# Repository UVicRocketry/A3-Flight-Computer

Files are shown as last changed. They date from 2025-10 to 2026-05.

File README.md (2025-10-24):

# A3-Flight-Computer
Hardware and software for Anduril-3 flight computer.

## Hardware 
All hardware is designed in KiCAD. If any footprints are added create a folder with the component name in the component-library folder and export all the files to there. when importing footprints and symbols add them to the A3-Flight-Computer library in KiCAD A3 Also add any datasheet and relevent documentation to this folder. 

## Software
All software will be stored in the A3-Flight-Computer-Software. (Rest of Organization TBD)

Various resources such as application notes, various datasheets etc will be stored in the resource folder

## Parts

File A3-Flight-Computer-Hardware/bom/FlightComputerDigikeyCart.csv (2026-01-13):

Index | Quantity | Part Number | Manufacturer Part Number | Description | Customer Reference | Available | Backorder | Unit Price | Extended Price CAD
1 | 2 | 670-1528-1-ND | ST1W008S4ER1500 | CONN MICRO SD CARD R/A SMD | J2 | 2 | 0 | 2.72000 | 5.44
2 | 2 | SER4070CT-ND | TSX-3225 16.0000MF18X-AC0 | CRYSTAL 16.0000MHZ 9PF SMD | Y1 | 2 | 0 | 0.57000 | 1.14
3 | 2 | XC2160CT-ND | ECS-.327-9-34QCS-TR | CRYSTAL 32.7680KHZ 9PF SMD | Y2 | 2 | 0 | 1.37000 | 2.74
4 | 2 | 497-STM32H523RET6-ND | STM32H523RET6 | IC MCU 32BIT 512KB FLASH 64LQFP | U1 | 2 | 0 | 7.17000 | 14.34
5 | 3 | AZ1117CH-3.3TRG1DICT-ND | AZ1117CH-3.3TRG1 | IC REG LINEAR 3.3V 1A SOT-223-3 | VR1 | 3 | 0 | 0.25000 | 0.75
6 | 2 | 2073-USB4105-GF-ACT-ND | USB4105-GF-A | CONN RCP USB2.0 TYP C 16P SMD RA | J3 | 2 | 0 | 1.13000 | 2.26
7 | 2 | 401-1999-1-ND | JS102011SAQN | SWITCH SLIDE SPDT 300MA 6V | SW1 | 2 | 0 | 1.10000 | 2.20
8 | 2 | 490-PKMCS0909E48H0-R1CT-ND | PKMCS0909E48H0-R1 | BUZZER PIEZO 2.5V 9X9MM W SMD | BZ1 | 2 | 0 | 1.63000 | 3.26
9 | 2 | IRLML0030TRPBFCT-ND | IRLML0030TRPBF | MOSFET N-CH 30V 5.3A SOT23 | Q1 | 2 | 0 | 0.72000 | 1.44
10 | 10 | 1655-DSS14UCT-ND | DSS14U | DIODE SCHOTTKY 40V 1A SOD123FL | D1, D2, D6 | 10 | 0 | 0.17100 | 1.71
11 | 2 | 160-1179-1-ND | LTST-C170GKT | LED GREEN CLEAR SMD | D4 | 2 | 0 | 0.15000 | 0.30
12 | 2 | 160-1413-1-ND | LTST-C170KFKT | LED ORANGE CLEAR SMD | D3 | 2 | 0 | 0.20000 | 0.40
13 | 2 | 296-TCAN3414DRCT-ND | TCAN3414DR | IC TRANSCEIVER HALF 1/1 8SOIC | U5 | 2 | 0 | 2.40000 | 4.80
14 | 2 | ADXL375BCCZ-RL7CT-ND | ADXL375BCCZ-RL7 | ACCELEROMETER 200G I2C/SPI 14LGA | U2 | 2 | 0 | 19.13000 | 38.26
15 | 2 | 497-LSM6DSO32CT-ND | LSM6DSO32TR | INEMO INERTIAL MODULE: 3D ACCELE | U3 | 2 | 0 | 5.40000 | 10.80
16 | 2 | 497-16265-1-ND | LPS22HBTR | SENSOR 18.27PSIA 24BIT 10HLGA | U4 | 2 | 0 | 3.78000 | 7.56
17 | 4 | 18-SMF54CACT-ND | SMF54CA | TVS DIODE 54VWM 87.1VC SOD123F | D7, D8 | 4 | 0 | 0.58000 | 2.32
18 | 3 | 2449-CS1213AGF260CT-ND | CS1213AGF260 | SWITCH TACTILE SPST-NO 0.05A 50V | Sw2 | 3 | 0 | 0.60000 | 1.80
19 | 4 | 1276-1244-1-ND | CL21A475KAQNNNE | CAP CER 4.7UF 25V X5R 0805 | C1 | 4 | 0 | 0.14000 | 0.56
20 | 3 | 1276-CL21A226MAYNNNECT-ND | CL21A226MAYNNNE | CAP CER 22UF 25V X5R 0805 | C8 | 3 | 0 | 0.12000 | 0.36
21 | 3 | 1276-2872-1-ND | CL21B106KOQNNNE | CAP CER 10UF 16V X7R 0805 | C9 | 3 | 0 | 0.12000 | 0.36
22 | 40 | 1276-1043-1-ND | CL05A104KA5NNNC | CAP CER 0.1UF 25V X5R 0402 | C2-7, C10, C17-24 | 40 | 0 | 0.00300 | 0.12
23 | 10 | 490-10012-1-ND | GRM155C80J225KE95D | CAP CER 2.2UF 6.3V X6S 0402 | C13, C14 | 10 | 0 | 0.07800 | 0.78
24 | 10 | 490-5926-1-ND | GRM1555C1H160JA01D | CAP CER 16PF 50V C0G/NP0 0402 | C15, C16 | 10 | 0 | 0.06400 | 0.64
25 | 10 | 1276-CL05C080DB51PNCCT-ND | CL05C080DB51PNC | CAP CER 8PF 50V C0G/NP0 0402 | C11, C12 | 10 | 0 | 0.04300 | 0.43
26 | 10 | 478-KGM05AR71E472KHCT-ND | KGM05AR71E472KH | CAP CER 4700PF 25V X7R 0402 | C25 | 10 | 0 | 0.03500 | 0.35
27 | 10 | P100KLCT-ND | ERJ-2RKF1003X | RES 100K OHM 1% 1/10W 0402 | R10 | 10 | 0 | 0.04300 | 0.43
28 | 10 | RMCF0402FT10K0CT-ND | RMCF0402FT10K0 | RES 10K OHM 1% 1/16W 0402 | R6 | 10 | 0 | 0.01100 | 0.11
29 | 10 | P100LCT-ND | ERJ-2RKF1000X | RES SMD 100 OHM 1% 1/10W 0402 | R9 | 10 | 0 | 0.04300 | 0.43
30 | 10 | P240LCT-ND | ERJ-2RKF2400X | RES SMD 240 OHM 1% 1/10W 0402 | R5, R7, R8 | 10 | 0 | 0.04300 | 0.43
31 | 6 | P5.1KDCCT-ND | ERA-2AEB512X | RES SMD 5.1K OHM 0.1% 1/16W 0402 | R1, R2 | 6 | 0 | 0.15000 | 0.90
32 | 10 | YAG3086CT-ND | RC0402FR-0727RL | RES 27 OHM 1% 1/16W 0402 | R3, R4 | 10 | 0 | 0.01100 | 0.11
33 | 10 | RMCF0402FT1K80CT-ND | RMCF0402FT1K80 | RES 1.8K OHM 1% 1/16W 0402 | R11, R12 | 10 | 0 | 0.00800 | 0.08
34 | 10 | 455-S2B-XH-A-ND | S2B-XH-A | CONN HEADER R/A 2POS 2.5MM | J1, J4, J6, J8 | 10 | 0 | 0.14800 | 1.48
35 | 3 | 455-S3B-XH-A-ND | S3B-XH-A | CONN HEADER R/A 3POS 2.5MM | J7 | 3 | 0 | 0.22000 | 0.66
36 | 2 | 160-1427-1-ND | LTST-C171KRKT | LED RED CLEAR SMD | D5 | 2 | 0 | 0.20000 | 0.40
37 | 10 | P59.0LCT-ND | ERJ-2RKF59R0X | RES SMD 59 OHM 1% 1/10W 0402 | R14, R13 | 10 | 0 | 0.04300 | 0.43
38 | 2 | 296-28778-1-ND | TLV1117LV33DCYR | IC REG LINEAR 3.3V 1A SOT-223-4 |  | 2 | 0 | 0.38656 | 0.78
39 | 10 | 1276-1029-1-ND | CL21B105KBFNNNE | CAP CER 1UF 50V X7R 0805 |  | 10 | 0 | 0.01859 | 0.19
40 | 2 | SAM8996-ND | TSW-104-07-F-D | CONN HEADER VERT 8POS 2.54MM | DEBUG | 2 | 0 | 0.62185 | 1.24

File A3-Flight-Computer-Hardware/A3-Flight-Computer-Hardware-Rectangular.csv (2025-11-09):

Reference | Qty | Value | DNP | Exclude from BOM | Exclude from Board | Footprint | Datasheet
BZ1 | 1 | Buzzer |  |  |  | Buzzer_Beeper:Buzzer_Murata_PKMCS0909E | ~
C1 | 1 | 4.7uF |  |  |  | Capacitor_SMD:C_0805_2012Metric
C2,C3,C4,C5,C6,C9,C16,C17,C18,C19,C20,C21,C22,C23 | 14 | 100nF |  |  |  | Capacitor_SMD:C_0805_2012Metric
C7 | 1 | 22uF |  |  |  | Capacitor_SMD:C_0805_2012Metric
C8 | 1 | 10uF |  |  |  | Capacitor_SMD:C_0805_2012Metric
C10,C11 | 2 | 8pF |  |  |  | Capacitor_SMD:C_0805_2012Metric
C12,C13 | 2 | 2.2uF |  |  |  | Capacitor_SMD:C_0805_2012Metric
C14 | 1 | 16pF |  |  |  | Capacitor_SMD:C_0805_2012Metric
C15 | 1 | 16pf |  |  |  | Capacitor_SMD:C_0805_2012Metric
C24 | 1 | 4.7nF |  |  |  | Capacitor_SMD:C_0805_2012Metric
D1,D2 | 2 | DSS14U |  |  |  | Diode_SMD:D_SOD-123
D3,D4 | 2 | LED |  |  |  | LED_SMD:LED_0805_2012Metric_Pad1.15x1.40mm_HandSolder | ~
D5 | 1 | SS14 |  |  |  | Diode_SMD:D_SMA | https://www.vishay.com/docs/88746/ss12.pdf
D6,D7 | 2 | SMF54CA |  |  |  | Diode_SMD:D_SMF | https://www.littelfuse.com/media?itemid=75e32973-b177-4ee3-a0ff-cedaf1abdb93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
J1 | 1 | BAT |  |  |  | Connector_JST:JST_XH_S2B-XH-A_1x02_P2.50mm_Horizontal | ~
J2 | 1 | ST1W008S4ER1500 |  |  |  | A3-Flight-Computer:JAE_ST1W008S4ER1500
J3 | 1 | USB_C_Receptacle_USB2.0_14P |  |  |  | Connector_USB:USB_C_Receptacle_Palconn_UTC16-G | https://www.usb.org/sites/default/files/documents/usb_type-c.zip
J4 | 1 | Debug Header |  |  |  | Connector_PinHeader_2.54mm:PinHeader_2x03_P2.54mm_Vertical | ~
J5 | 1 | Cam 1 |  |  |  | Connector_JST:JST_XH_B2B-XH-A_1x02_P2.50mm_Vertical | ~
J6 | 1 | Cam 2 |  |  |  | Connector_JST:JST_XH_B2B-XH-A_1x02_P2.50mm_Vertical | ~
J8 | 1 | Telem |  |  |  | Connector_JST:JST_XH_B3B-XH-A_1x03_P2.50mm_Vertical | ~
J9 | 1 | CAN |  |  |  | Connector_JST:JST_XH_S2B-XH-A_1x02_P2.50mm_Horizontal | ~
Q1 | 1 | IRLML0030 |  |  |  | Package_TO_SOT_SMD:SOT-23 | https://www.infineon.com/dgdl/irlml0030pbf.pdf?fileId=5546d462533600a401535664773825df
R1,R2 | 2 | 5.1K |  |  |  | Resistor_SMD:R_0805_2012Metric | ~
R3,R4 | 2 | 27R |  |  |  | Resistor_SMD:R_0805_2012Metric | ~
R5,R7 | 2 | 240R |  |  |  | Resistor_SMD:R_0805_2012Metric | ~
R6 | 1 | 10k |  |  |  | Resistor_SMD:R_0805_2012Metric | ~
R8 | 1 | 100 |  |  |  | Resistor_SMD:R_0805_2012Metric | ~
R9 | 1 | 100k |  |  |  | Resistor_SMD:R_0805_2012Metric | ~
R10,R11 | 2 | 1.8k |  |  |  | Resistor_SMD:R_0805_2012Metric | ~
R12,R13 | 2 | 60 |  |  |  | Resistor_SMD:R_0805_2012Metric | ~
SW1 | 1 | BOOT |  |  |  | Button_Switch_SMD:SW_SPDT_CK_JS102011SAQN | ~
SW2 | 1 | RST |  |  |  | Button_Switch_SMD:SW_SPST_TS-1088-xR025 | ~
U1 | 1 | STM32H523RETx |  |  |  | Package_QFP:LQFP-64_10x10mm_P0.5mm | https://www.st.com/resource/en/datasheet/stm32h523re.pdf
U2 | 1 | ADXL375BCCZ-RL7 |  |  |  | A3-Flight-Computer:LGA_CC-14-1_ADI | https://www.analog.com/media/en/technical-documentation/data-sheets/ADXL375-EP.pdf
U3 | 1 | LSM6DSO32TR |  |  |  | A3-Flight-Computer:XDCR_LSM6DSO32TR
U4 | 1 | LPS22HBTR |  |  |  | A3-Flight-Computer:PQFN50P200X200X80-10N
U5 | 1 | PTCAN3414DR |  |  |  | A3-Flight-Computer:SOIC8_D_TEX | https://www.ti.com/lit/gpn/tcan3414
VR1 | 1 | AZ1117CH-3.3TRG1 |  |  |  | A3-Flight-Computer:VREG_AZ1117CH-3.3TRG1
Y1 | 1 | TSX-3225_16.0000MF18X-AC0 |  |  |  | A3-Flight-Computer:XTAL_TSX-3225_16.0000MF18X-AC0
Y2 | 1 | ECS-.327-9-34QCS-TR |  |  |  | A3-Flight-Computer:XTAL_ECS-.327-9-34QCS-TR

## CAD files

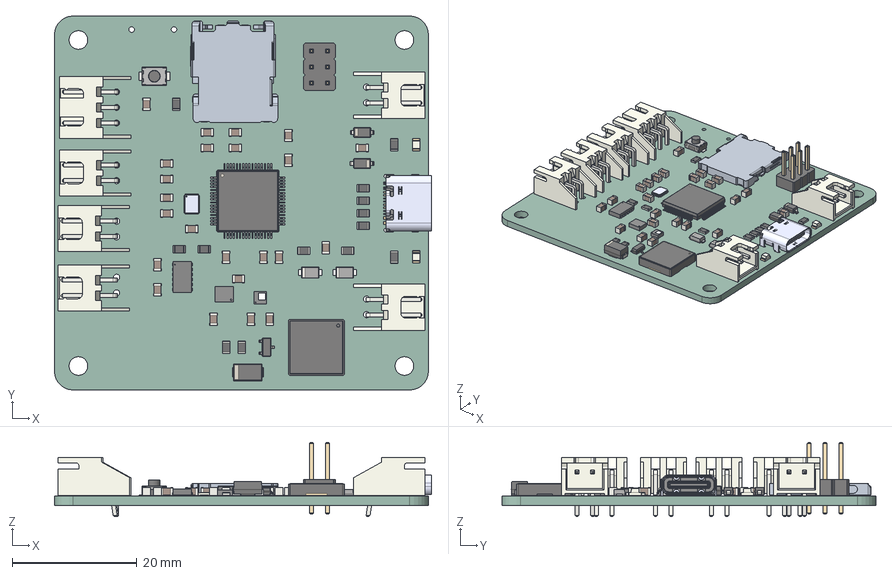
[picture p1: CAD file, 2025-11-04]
A3-Flight-Computer-Hardware/alt-design/A3-Flight-Computer-Hardware.step
60.5 x 60.0 x 11.9 mm
C_0805_2012Metric x 23
LSM6DSO32TR
R_0805_2012Metric x 13
TSX-3225_16.0000MF18X-AC0
SW_SPST_TS-1088-xR025
USB4105GFA_USB4105GFA
JST_XH_S2B-XH-A_1x02_P2.50mm_Horizontal x 5
D_SMF x 2
D_SOD-123 x 2
ST1W008S4E-V1_JAE_Proprietary
PinHeader_2x03_P2.54mm_Vertical
LED_0805_2012Metric x 2
JST_XH_S3B-XH-A_1x03_P2.50mm_Horizontal
LQFP-64_10x10mm_P0.5mm
Buzzer_Murata_PKMCS0909E
LGA_CC-14-1_ADI
LPS22HBTR
SOT-23
D_SMA
A3-Flight-Computer-Hardware_PCB

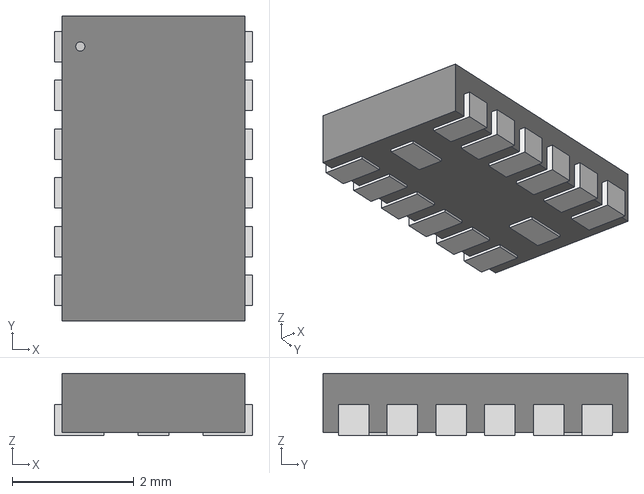
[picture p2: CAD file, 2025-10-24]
A3-Flight-Computer-Hardware/component-library/ADXL375/LGA_CC-14-1_ADI.step
3.25 x 5.00 x 1.02 mm

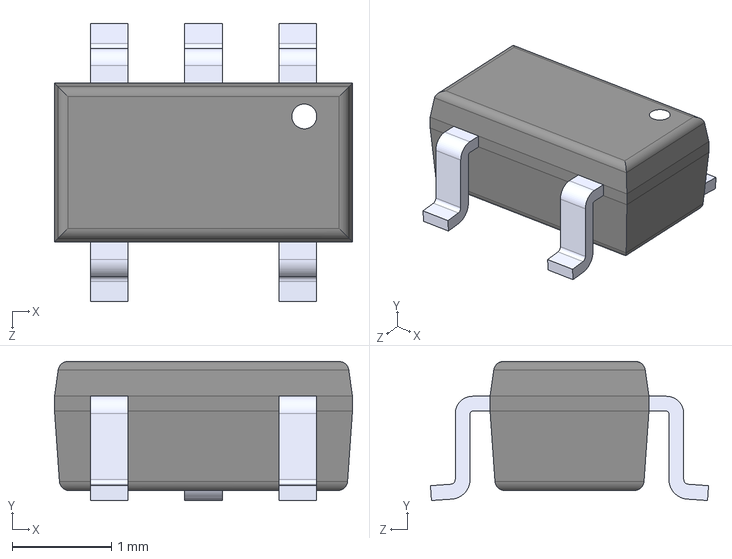
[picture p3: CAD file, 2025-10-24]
A3-Flight-Computer-Hardware/component-library/AP2112K-3.3TRG1/AP2112K-3.3TRG1.step
3.00 x 1.40 x 2.80 mm

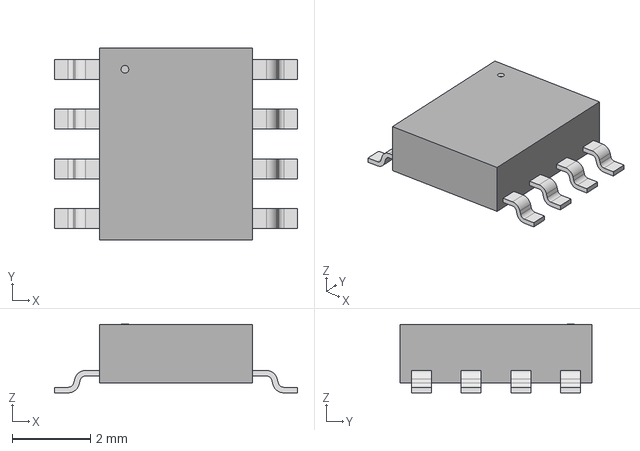
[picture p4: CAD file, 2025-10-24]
A3-Flight-Computer-Hardware/component-library/ATA6561/SOIC8_4P9X3P9MC_MCH.step
6.20 x 4.90 x 1.75 mm

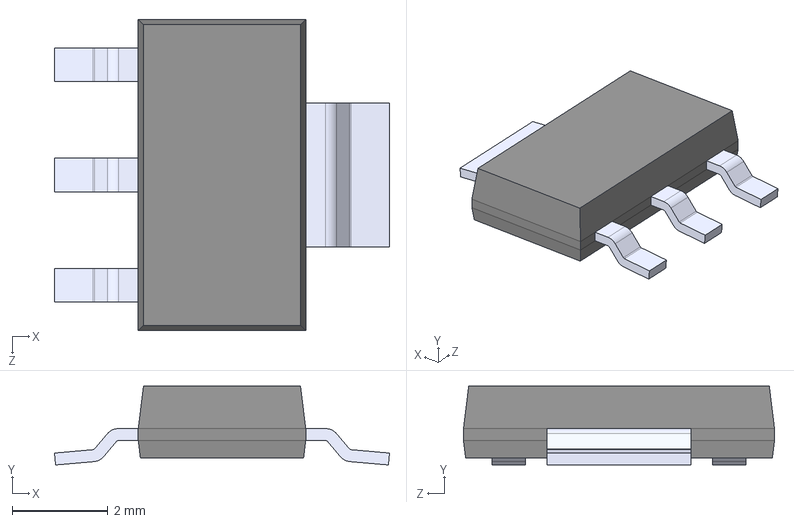
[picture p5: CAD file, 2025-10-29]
A3-Flight-Computer-Hardware/component-library/AZ1117CH-3.3TRG1/AZ1117CH-3.3TRG1.step
7.00 x 1.65 x 6.50 mm

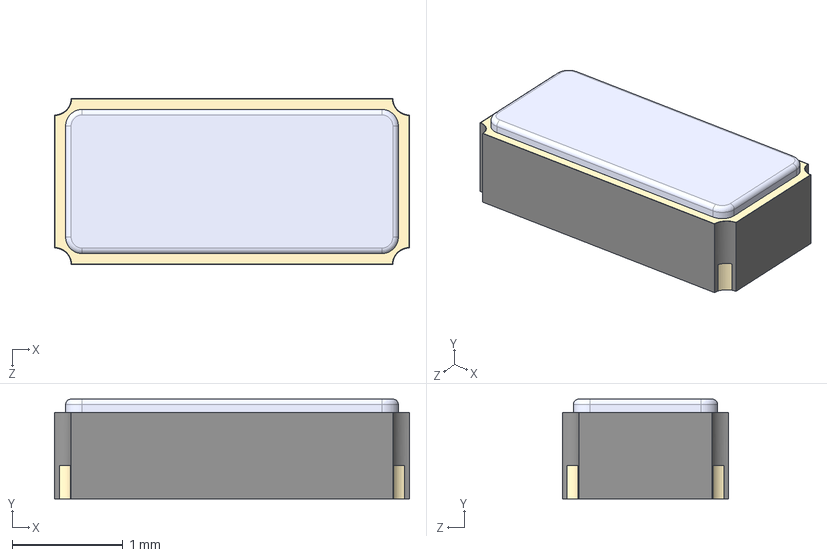
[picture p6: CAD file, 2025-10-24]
A3-Flight-Computer-Hardware/component-library/ECS-327-9-34QCS-TR/ECS-.327-9-34QCS-TR.step
3.20 x 0.9 x 1.50 mm

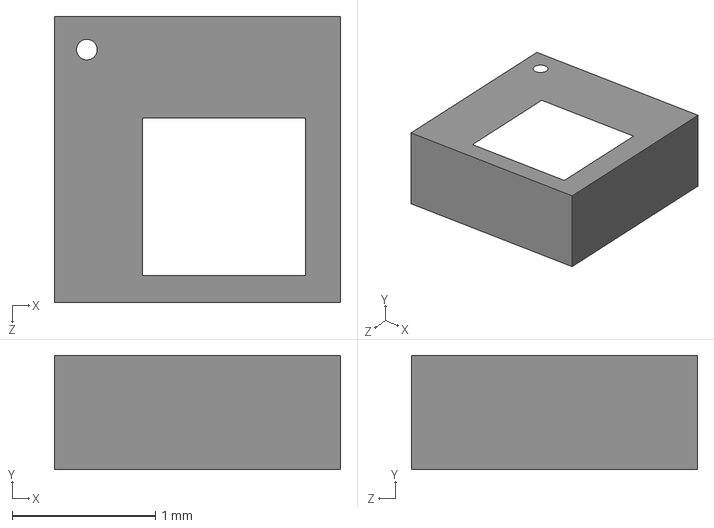
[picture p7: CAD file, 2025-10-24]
A3-Flight-Computer-Hardware/component-library/LPS22HBTR/LPS22HBTR.step
2.00 x 0.8 x 2.00 mm

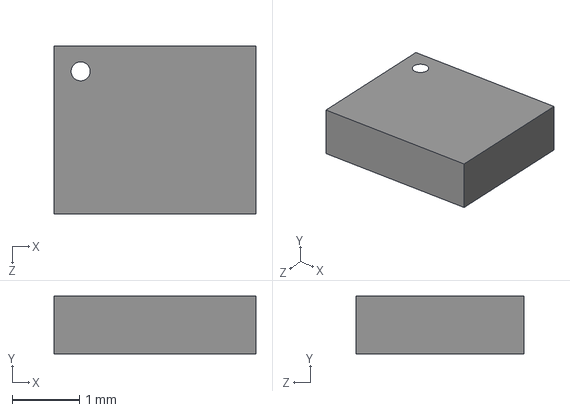
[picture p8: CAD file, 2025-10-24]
A3-Flight-Computer-Hardware/component-library/LSM6DSO32TR/LSM6DSO32TR.step
3.00 x 0.86 x 2.50 mm

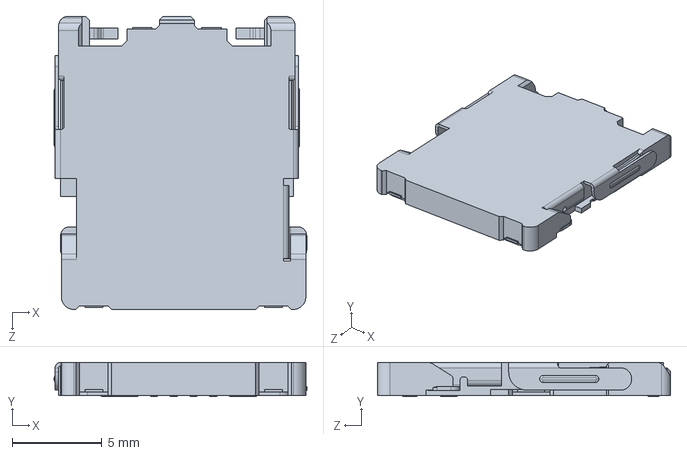
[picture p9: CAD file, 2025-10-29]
A3-Flight-Computer-Hardware/component-library/STW008S4ER1500/ST1W008S4E-V1_JAE_Proprietary.step
14.0 x 1.90 x 16.3 mm

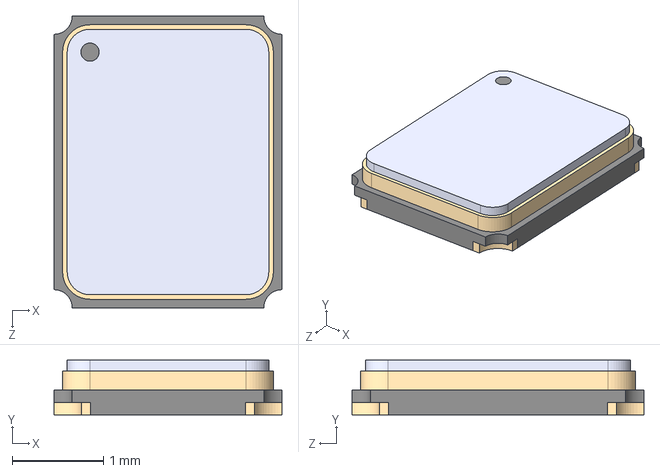
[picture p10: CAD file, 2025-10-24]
A3-Flight-Computer-Hardware/component-library/TSX-3225/TSX-3225_16.0000MF18X-AC0.step
2.50 x 0.6 x 3.20 mm

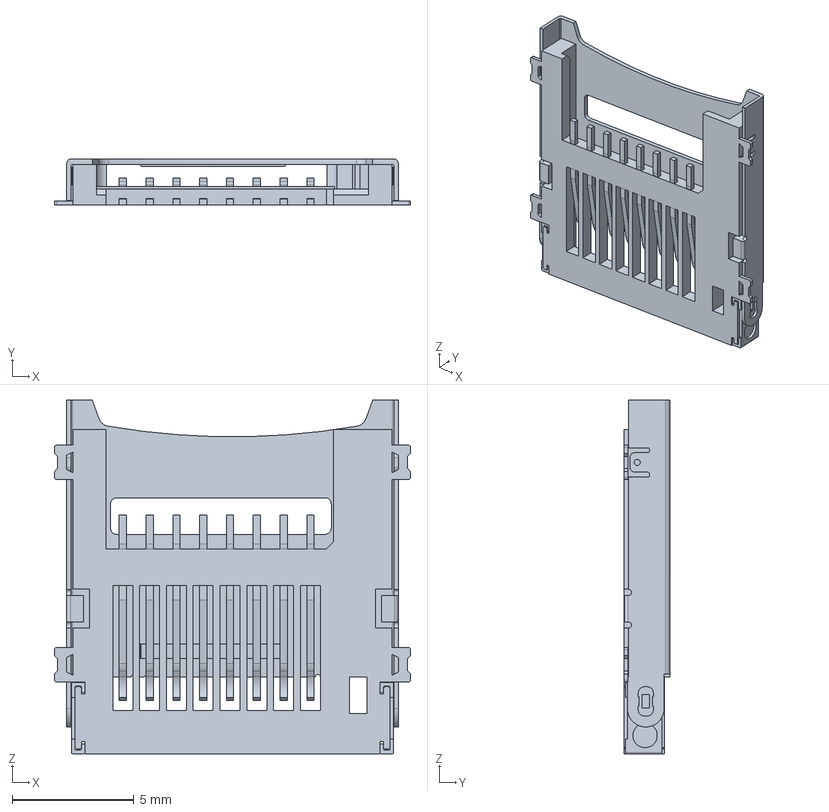
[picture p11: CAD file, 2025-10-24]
A3-Flight-Computer-Hardware/component-library/472192001.stp
14.6 x 1.90 x 14.5 mm

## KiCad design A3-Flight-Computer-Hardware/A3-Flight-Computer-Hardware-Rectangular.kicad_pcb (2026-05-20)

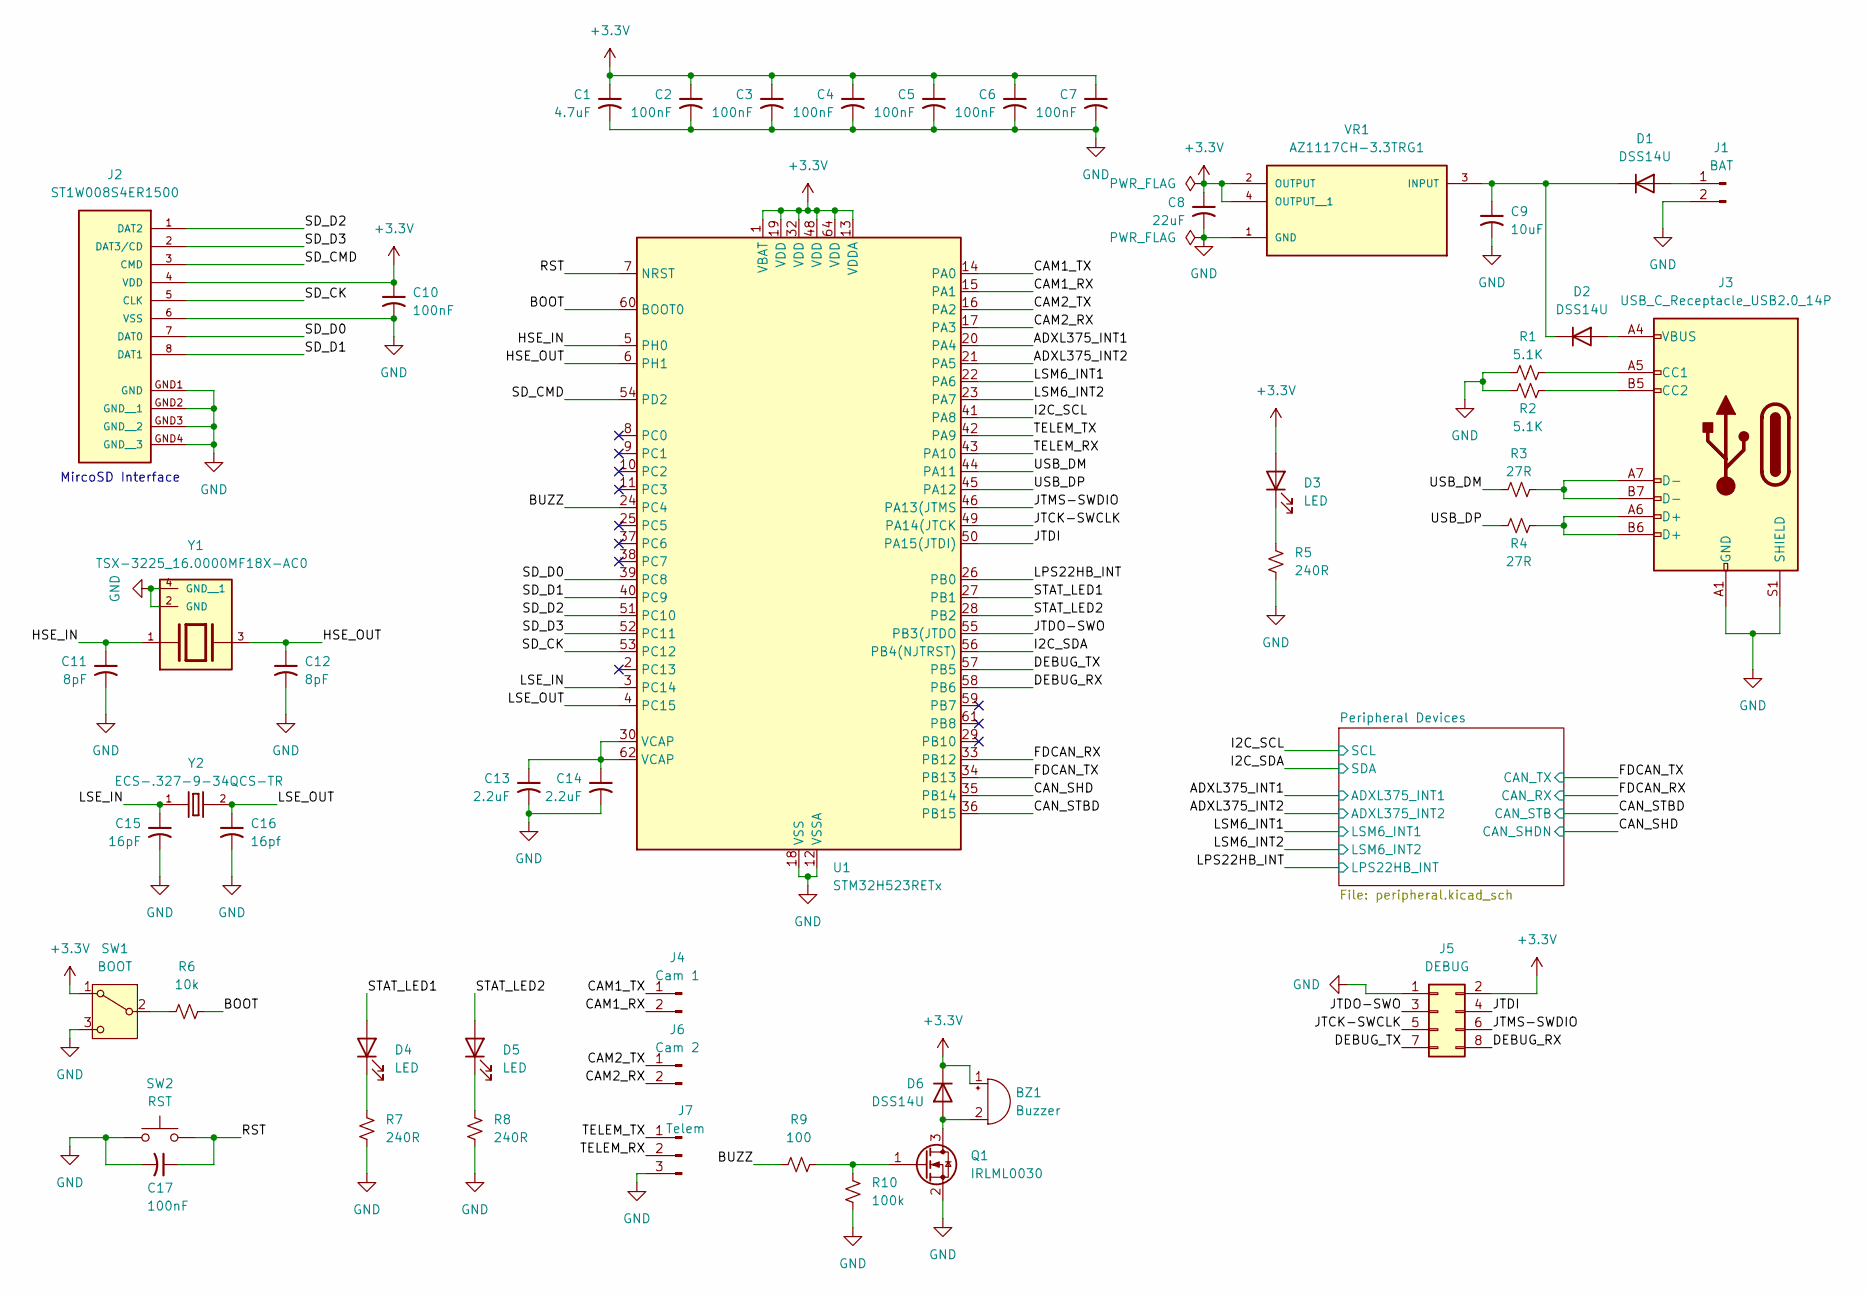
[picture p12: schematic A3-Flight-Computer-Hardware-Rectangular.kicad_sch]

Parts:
BZ1: Buzzer; Buzzer_Murata_PKMCS0909E
C1: 4.7uF; C_0805_2012Metric
C2, C3, C4, C5, C6, C7, C10, C17: 100nF; C_0402_1005Metric
C8: 22uF; C_0805_2012Metric
C9: 10uF; C_0805_2012Metric
C11, C12: 8pF; C_0402_1005Metric
C13, C14: 2.2uF; C_0402_1005Metric
C15: 16pF; C_0402_1005Metric
C16: 16pf; C_0402_1005Metric
D1, D2, D6: DSS14U; D_SOD-123
D3, D4, D5: LED; LED_0805_2012Metric_Pad1.15x1.40mm_HandSolder
J1: BAT; JST_XH_S2B-XH-A_1x02_P2.50mm_Horizontal
J2: ST1W008S4ER1500; JAE_ST1W008S4ER1500; PARTREV 2
J3: USB_C_Receptacle_USB2.0_14P; USB_C_Receptacle_Palconn_UTC16-G
J4: Cam 1; JST_XH_S2B-XH-A_1x02_P2.50mm_Horizontal
J5: DEBUG; PinHeader_2x04_P2.54mm_Vertical
J6: Cam 2; JST_XH_S2B-XH-A_1x02_P2.50mm_Horizontal
J7: Telem; JST_XH_S3B-XH-A_1x03_P2.50mm_Horizontal
Q1: IRLML0030; SOT-23
R1, R2: 5.1K; R_0402_1005Metric
R3, R4: 27R; R_0402_1005Metric
R5, R7, R8: 240R; R_0402_1005Metric
R6: 10k; R_0402_1005Metric
R9: 100; R_0402_1005Metric
R10: 100k; R_0402_1005Metric
SW1: BOOT; SW_SPDT_CK_JS102011SAQN
SW2: RST; SW_SPST_TS-1088-xR025
U1: STM32H523RETx; LQFP-64_10x10mm_P0.5mm
VR1: AZ1117CH-3.3TRG1; VREG_AZ1117CH-3.3TRG1; PARTREV 5 - 2
Y1: TSX-3225_16.0000MF18X-AC0; XTAL_TSX-3225_16.0000MF18X-AC0; PARTREV N/A
Y2: ECS-.327-9-34QCS-TR; XTAL_ECS-.327-9-34QCS-TR; PARTREV 2018

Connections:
+3.3V: BZ1.1 (+), C1.1, C2.1, C3.1, C4.1, C5.1, C6.1, C7.1, C8.1, C10.1, D3.2 (A), D6.1 (K), J2.4 (VDD), J5.2, SW1.1 (A), U1.1 (VBAT), U1.13 (VDDA), U1.19 (VDD), U1.32 (VDD), U1.48 (VDD), U1.64 (VDD), VR1.2 (OUTPUT), VR1.4 (OUTPUT__1); also elsewhere on the board
/ADXL375_INT1: U1.20 (PA4); also elsewhere on the board
/ADXL375_INT2: U1.21 (PA5); also elsewhere on the board
/BOOT: R6.2, U1.60 (BOOT0)
/BUZZ: R9.1, U1.24 (PC4)
/CAM1_RX: J4.2, U1.15 (PA1)
/CAM1_TX: J4.1, U1.14 (PA0)
/CAM2_RX: J6.2, U1.17 (PA3)
/CAM2_TX: J6.1, U1.16 (PA2)
/CAN_SHD: U1.35 (PB14); also elsewhere on the board
/CAN_STBD: U1.36 (PB15); also elsewhere on the board
/DEBUG_RX: J5.8, U1.58 (PB6)
/DEBUG_TX: J5.7, U1.57 (PB5)
/FDCAN_RX: U1.33 (PB12); also elsewhere on the board
/FDCAN_TX: U1.34 (PB13); also elsewhere on the board
/HSE_IN: C11.1, U1.5 (PH0), Y1.1
/HSE_OUT: C12.1, U1.6 (PH1), Y1.3
/I2C_SCL: U1.41 (PA8); also elsewhere on the board
/I2C_SDA: U1.56 (PB4(NJTRST)); also elsewhere on the board
/JTCK-SWCLK: J5.5, U1.49 (PA14(JTCK)
/JTDI: J5.4, U1.50 (PA15(JTDI))
/JTDO-SWO: J5.3, U1.55 (PB3(JTDO)
/JTMS-SWDIO: J5.6, U1.46 (PA13(JTMS)
/LPS22HB_INT: U1.26 (PB0); also elsewhere on the board
/LSE_IN: C15.1, U1.3 (PC14), Y2.1
/LSE_OUT: C16.1, U1.4 (PC15), Y2.2
/LSM6_INT1: U1.22 (PA6); also elsewhere on the board
/LSM6_INT2: U1.23 (PA7); also elsewhere on the board
/RST: C17.1, SW2.2, U1.7 (NRST)
/SD_CK: J2.5 (CLK), U1.53 (PC12)
/SD_CMD: J2.3 (CMD), U1.54 (PD2)
/SD_D0: J2.7 (DAT0), U1.39 (PC8)
/SD_D1: J2.8 (DAT1), U1.40 (PC9)
/SD_D2: J2.1 (DAT2), U1.51 (PC10)
/SD_D3: J2.2 (DAT3/CD), U1.52 (PC11)
/STAT_LED1: D4.2 (A), U1.27 (PB1)
/STAT_LED2: D5.2 (A), U1.28 (PB2)
/TELEM_RX: J7.2, U1.43 (PA10)
/TELEM_TX: J7.1, U1.42 (PA9)
/USB_DM: R3.1, U1.44 (PA11)
/USB_DP: R4.1, U1.45 (PA12)
GND: C1.2, C2.2, C3.2, C4.2, C5.2, C6.2, C7.2, C8.2, C9.2, C10.2, C11.2, C12.2, C13.2, C14.2, C15.2, C16.2, C17.2, J1.2, J2.6 (VSS), J2.GND1 (GND), J2.GND2 (GND__1), J2.GND3 (GND__2), J2.GND4 (GND__3), J3.A1 (GND), J3.A12 (GND), J3.B1 (GND), J3.B12 (GND), J3.S1 (SHIELD), J5.1, J7.3, Q1.2 (S), R1.1, R2.1, R5.1, R7.1, R8.1, R10.1, SW1.3 (C), SW2.1, U1.12 (VSSA), U1.18 (VSS), U1.31 (VSS), U1.47 (VSS), U1.63 (VSS), VR1.1 (GND), Y1.2 (GND), Y1.4 (GND__1); also elsewhere on the board
unnamed: BZ1.2 (-), D6.2 (A), Q1.3 (D)
unnamed: C13.1, C14.1, U1.30 (VCAP), U1.62 (VCAP)
unnamed: D1.2 (A), J1.1
unnamed: C9.1, D1.1 (K), D2.1 (K), VR1.3 (INPUT)
unnamed: D2.2 (A), J3.A4 (VBUS), J3.A9 (VBUS), J3.B4 (VBUS), J3.B9 (VBUS)
unnamed: D3.1 (K), R5.2
unnamed: D4.1 (K), R7.2
unnamed: D5.1 (K), R8.2
unnamed: J3.A5 (CC1), R1.2
unnamed: J3.B5 (CC2), R2.2
unnamed: J3.A6 (D+), J3.B6 (D+), R4.2
unnamed: J3.A7 (D-), J3.B7 (D-), R3.2
unnamed: Q1.1 (G), R9.2, R10.2
unnamed: R6.1, SW1.2 (B)

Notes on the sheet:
MircoSD Interface

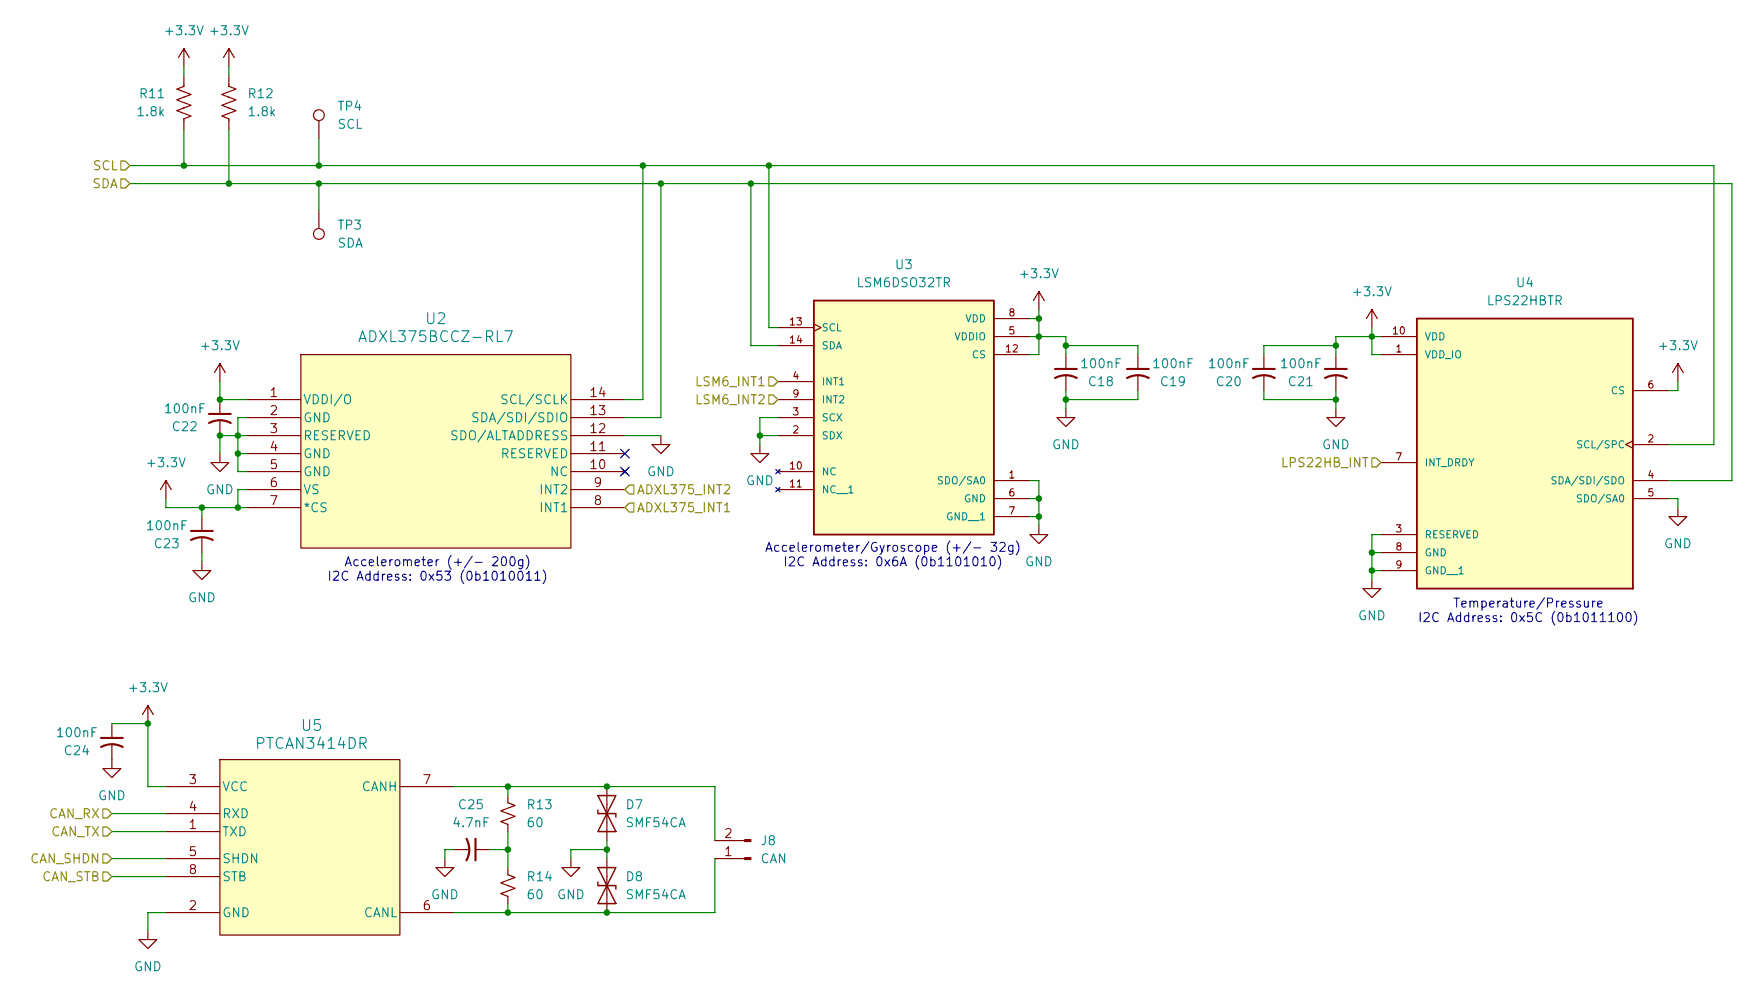
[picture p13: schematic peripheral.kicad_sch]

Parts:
C18, C19, C20, C21, C22, C23, C24: 100nF; C_0402_1005Metric
C25: 4.7nF; C_0402_1005Metric
D7, D8: SMF54CA; D_SMF
J8: CAN; JST_XH_S2B-XH-A_1x02_P2.50mm_Horizontal
R11, R12: 1.8k; R_0402_1005Metric
R13, R14: 60; R_0402_1005Metric
TP3: SDA; TestPoint_THTPad_1.0x1.0mm_Drill0.5mm
TP4: SCL; TestPoint_THTPad_1.0x1.0mm_Drill0.5mm
U2: ADXL375BCCZ-RL7; LGA_CC-14-1_ADI
U3: LSM6DSO32TR; XDCR_LSM6DSO32TR; PARTREV 1
U4: LPS22HBTR; PQFN50P200X200X80-10N; PARTREV 6
U5: PTCAN3414DR; SOIC8_D_TEX

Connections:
+3.3V: C18.1, C19.1, C20.1, C21.1, C22.1, C23.1, C24.1, R11.1, R12.1, U2.1 (VDDI/O), U2.6 (VS), U2.7 (*CS), U3.5 (VDDIO), U3.8 (VDD), U3.12 (CS), U4.1 (VDD_IO), U4.6 (CS), U4.10 (VDD), U5.3 (VCC); also elsewhere on the board
/ADXL375_INT1: U2.8 (INT1); also elsewhere on the board
/ADXL375_INT2: U2.9 (INT2); also elsewhere on the board
/CAN_SHD: U5.5 (SHDN); also elsewhere on the board
/CAN_STBD: U5.8 (STB); also elsewhere on the board
/FDCAN_RX: U5.4 (RXD); also elsewhere on the board
/FDCAN_TX: U5.1 (TXD); also elsewhere on the board
/I2C_SCL: R11.2, TP4.1, U2.14 (SCL/SCLK), U3.13 (SCL), U4.2 (SCL/SPC); also elsewhere on the board
/I2C_SDA: R12.2, TP3.1, U2.13 (SDA/SDI/SDIO), U3.14 (SDA), U4.4 (SDA/SDI/SDO); also elsewhere on the board
/LPS22HB_INT: U4.7 (INT_DRDY); also elsewhere on the board
/LSM6_INT1: U3.4 (INT1); also elsewhere on the board
/LSM6_INT2: U3.9 (INT2); also elsewhere on the board
GND: C18.2, C19.2, C20.2, C21.2, C22.2, C23.2, C24.2, C25.2, D7.2 (A2), D8.1 (A1), U2.2 (GND), U2.3 (RESERVED), U2.4 (GND), U2.5 (GND), U2.12 (SDO/ALTADDRESS), U3.1 (SDO/SA0), U3.2 (SDX), U3.3 (SCX), U3.6 (GND), U3.7 (GND__1), U4.3 (RESERVED), U4.5 (SDO/SA0), U4.8 (GND), U4.9 (GND__1), U5.2 (GND); also elsewhere on the board
unnamed: C25.1, R13.1, R14.2
unnamed: D7.1 (A1), J8.2, R13.2, U5.7 (CANH)
unnamed: D8.2 (A2), J8.1, R14.1, U5.6 (CANL)

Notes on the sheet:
Accelerometer (+/- 200g) I2C Address: 0x53 (0b1010011)
Temperature/Pressure I2C Address: 0x5C (0b1011100)
Accelerometer/Gyroscope (+/- 32g) I2C Address: 0x6A (0b1101010)

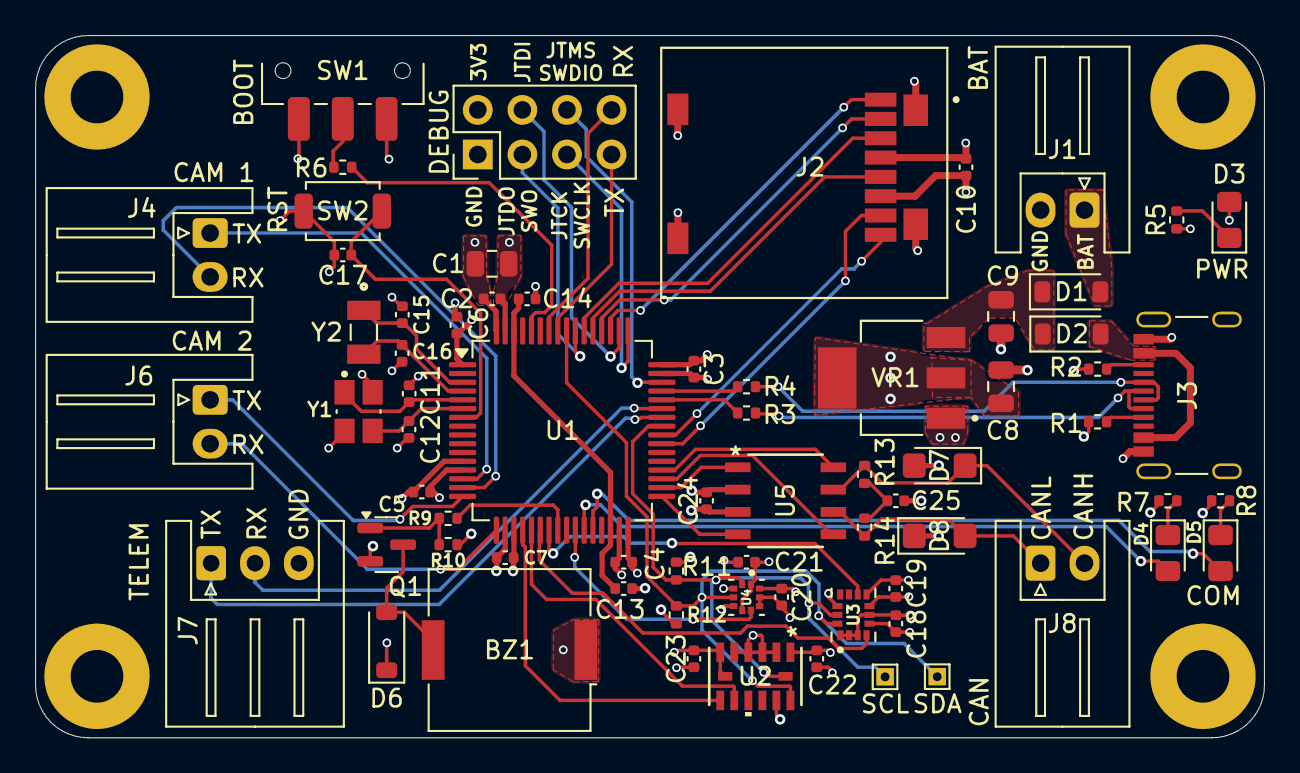
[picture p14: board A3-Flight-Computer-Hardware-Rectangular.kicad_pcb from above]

Board: 4 copper layers, 70.0 x 40.0 mm, 69 parts (0 on the bottom side), 59 nets.

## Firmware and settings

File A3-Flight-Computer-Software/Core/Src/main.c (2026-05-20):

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
/* Includes ------------------------------------------------------------------*/
#include "main.h"
#include "app_filex.h"
#include "stm32h5xx_hal_sd.h"
#include "stm32h5xx_ll_sdmmc.h"


FDCAN_HandleTypeDef hfdcan2;

I2C_HandleTypeDef hi2c3;

SD_HandleTypeDef hsd1;

TIM_HandleTypeDef htim2;

UART_HandleTypeDef huart4;
UART_HandleTypeDef huart5;
UART_HandleTypeDef huart1;
UART_HandleTypeDef huart2;

PCD_HandleTypeDef hpcd_USB_DRD_FS;

void SystemClock_Config(void);
static void MX_GPIO_Init(void);
static void MX_FDCAN2_Init(void);
static void MX_SDMMC1_SD_Init(void);
static void MX_UART4_Init(void);
static void MX_UART5_Init(void);
static void MX_USART1_UART_Init(void);
static void MX_USART2_UART_Init(void);
static void MX_USB_PCD_Init(void);
static void MX_I2C3_Init(void);
static void MX_TIM2_Init(void);
/* USER CODE BEGIN 0 */

FX_MEDIA sd_card;
uint32_t card_memory[FX_STM32_SD_DEFAULT_SECTOR_SIZE/sizeof(uint32_t)];

/* USER CODE END 0 */

/**
  * @brief  The application entry point.
  * @retval int
  */
int main(void)
{

  /* MCU Configuration--------------------------------------------------------*/

  /* Reset of all peripherals, Initializes the Flash interface and the Systick. */
  HAL_Init();

  /* Configure the system clock */
  SystemClock_Config();

  /* Initialize all configured peripherals */
  MX_GPIO_Init();
  MX_FDCAN2_Init();
  MX_SDMMC1_SD_Init();
  MX_UART4_Init();
  MX_UART5_Init();
  MX_USART1_UART_Init();
  MX_USART2_UART_Init();
  MX_USB_PCD_Init();
  MX_I2C3_Init();
  MX_TIM2_Init();
  MX_FileX_Init();
  /* USER CODE BEGIN 2 */

  uint32_t status = 0;
  uint32_t size = sizeof(card_memory);

  uint8_t buffer[512];
  uint8_t card_name[] = "SD_LOG";

  HAL_SD_CardStatusTypeDef pStatus;
  HAL_SD_CardInfoTypeDef pCardInfo;

  status = HAL_SD_Init(&hsd1);
  status = HAL_SD_ConfigWideBusOperation(&hsd1, SDMMC_BUS_WIDE_4B);
  status = HAL_SD_ConfigSpeedBusOperation(&hsd1, SDMMC_SPEED_MODE_AUTO);

  status = HAL_SD_GetCardStatus(&hsd1, &pStatus);
  HAL_SD_StateTypeDef state = HAL_SD_GetCardState(&hsd1);
  status = HAL_SD_GetCardInfo(&hsd1, &pCardInfo);

  // status = HAL_SD_ReadBlocks(&hsd1, buffer, 0x00, 1, 1000);

  //status = fx_media_format(&sd_card, fx_stm32_sd_driver, 0, (VOID *) card_memory, sizeof(card_memory), "STM32_SDIO_DISK",1,0,0,122265600,512,1,1,1);

  status =  fx_media_open(
    &sd_card, 
    &card_name[0], 
    fx_stm32_sd_driver, 
    0,
    (VOID *) card_memory, 
    sizeof(card_memory));
  /* USER CODE END 2 */

  /* Infinite loop */
  /* USER CODE BEGIN WHILE */
  while (1)
  {
    /* USER CODE END WHILE */

    /* USER CODE BEGIN 3 */
  }
  /* USER CODE END 3 */
}

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


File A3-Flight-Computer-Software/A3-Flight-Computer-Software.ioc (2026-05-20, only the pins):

Mcu.UserName=STM32H523RCTx
PA0.Signal=UART4_TX
PA1.Signal=UART4_RX
PA10.Signal=USART1_RX
PA11.Signal=USB_DM
PA12.Signal=USB_DP
PA13(JTMS/SWDIO).Signal=DEBUG_JTMS-SWDIO
PA14(JTCK/SWCLK).Signal=DEBUG_JTCK-SWCLK
PA15(JTDI).Signal=DEBUG_JTDI
PA2.Signal=USART2_TX
PA3.Signal=USART2_RX
PA4.Signal=GPXTI4
PA5.Signal=GPXTI5
PA6.Signal=GPXTI6
PA7.Signal=GPXTI7
PA8.Signal=I2C3_SCL
PA9.Signal=USART1_TX
PB0.Signal=GPXTI0
PB12.Signal=FDCAN2_RX
PB13.Signal=FDCAN2_TX
PB14.Signal=GPIO_Output
PB15.Signal=GPIO_Output
PB2.Signal=GPIO_Output
PB3(JTDO/TRACESWO).Signal=DEBUG_JTDO-SWO
PB4(NJTRST).Signal=I2C3_SDA
PB5.Signal=UART5_RX
PB6.Signal=UART5_TX
PB7.Signal=FDCAN1_TX
PC10.Signal=SDMMC1_D2
PC11.Signal=SDMMC1_D3
PC12.Signal=SDMMC1_CK
PC14-OSC32_IN(OSC32_IN).Signal=RCC_OSC32_IN
PC15-OSC32_OUT(OSC32_OUT).Signal=RCC_OSC32_OUT
PC4.Signal=S_TIM2_CH4
PC8.Signal=SDMMC1_D0
PC9.Signal=SDMMC1_D1
PD2.Signal=SDMMC1_CMD
PH0-OSC_IN(PH0).Signal=RCC_OSC_IN
PH1-OSC_OUT(PH1).Signal=RCC_OSC_OUT

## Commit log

2025-10-24 Initial Repository Setup
    [472192001.stp, A3-Flight-Computer-Hardware.kicad_pcb, A3-Flight-Computer-Hardware.kicad_sch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]
2025-10-29 Initial schematic
    [A3-Flight-Computer-Hardware.kicad_pcb, A3-Flight-Computer-Hardware.kicad_sch, AZ1117CH-3.3TRG1.step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]
2025-11-04 First PCB revision
    [A3-Flight-Computer-Hardware.kicad_pcb, A3-Flight-Computer-Hardware.kicad_sch, A3-Flight-Computer-Hardware.step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]
2025-11-09 Adjusted PCB Dimensions
    [A3-Flight-Computer-Hardware-Rectangular-B_Cu.gbr, A3-Flight-Computer-Hardware-Rectangular-B_Mask.gbr, A3-Flight-Computer-Hardware-Rectangular-B_Paste.gbr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]
2025-11-20 Small routing changes
    [A3-Flight-Computer-Hardware-Rectangular.kicad_pcb, A3-Flight-Computer-Hardware-Rectangular.kicad_sch, A3-Flight-Computer-Hardware-Rectangular.step]
2025-12-07 Added labels and changed component sizes
    [A3-Flight-Computer-Hardware-Rectangular-B_Cu.gbr, A3-Flight-Computer-Hardware-Rectangular-B_Mask.gbr, A3-Flight-Computer-Hardware-Rectangular-B_Paste.gbr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]
2026-01-13 Updated gerber files + BOM for purchasing
    [A3-Flight-Computer-Hardware-Rectangular-B_Cu.gbr, A3-Flight-Computer-Hardware-Rectangular-B_Mask.gbr, A3-Flight-Computer-Hardware-Rectangular-B_Paste.gbr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]
2026-05-20 Updated STM32CubeMX board Config
    [A3-Flight-Computer-Hardware-Rectangular.kicad_pcb, A3-Flight-Computer-Hardware-Rectangular.kicad_sch, peripheral.kicad_sch]
2026-05-28 Added FatFs driver

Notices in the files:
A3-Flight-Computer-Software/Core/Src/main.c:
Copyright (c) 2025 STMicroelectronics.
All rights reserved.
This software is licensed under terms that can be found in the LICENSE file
